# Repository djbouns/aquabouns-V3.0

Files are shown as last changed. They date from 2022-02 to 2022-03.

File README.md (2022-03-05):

# Aquabouns-V3.0

#### l'Aquabouns, le programme entièrement GRATUIT d'automatisation d'aquarium récifal.

 *-*-*-*-*
 
 *-*-*-*-* *-*-*-*-* *-*-*-*-* *-*-*-*-* *-*-*-*-* *-*-*-*-* *-*-*-*-* *-*-*-*-* *-*-*-*-* *-*-*-*-* *-*-*-*-* *-*-*-*-*
 
 *-*-*-*-*
 
###### l’Aquabouns en questions:  
> l'Aquabouns c'est quoi ? ----------------------- l'Aquabouns est un programme pour automatiser votre aquarium récifal. 
> 
> Comment ça fonctionne ?------------------------- le programme Aquabouns est prévu pour etre instalé sur une cartes arduino Mega. l'arduino communique ensuite avec différents périphériques (écran, module wifi et module GSM) et interprète l'état des différents capteurs (flotteur, sonde de température, horloge) et en fonction du paramétrage, intervient sur le matériel du bac (pompe remonté, brassage, ventilation, écumeur ...). 
> 
> Comment obtenir le programme ? à quel prix ? --- l'Aquabouns est mis a disposition GRATUITEMENT, il a été déposé sous License libre (GPL 3.0) afin que tout le monde puisse en profiter. 
> 
> Comment faire le montage ? --------------------- Tout se trouve dans les notices que vous pouvez télécharger sur www.aquabouns.fr et si le montage n'est pas à votre porté, vous pouvez vous faire aider d'un PCBouns, www.pcbouns.fr. 

 *-*-*-*-*
 
 *-*-*-*-* *-*-*-*-* *-*-*-*-* *-*-*-*-* *-*-*-*-* *-*-*-*-* *-*-*-*-* *-*-*-*-* *-*-*-*-* *-*-*-*-* *-*-*-*-* *-*-*-*-*
 
 *-*-*-*-*
 
#### Soutenez le projet pour qu'il continue d’évoluer et d’être mis à disposition gratuitement en faisant un DON

 

 *-*-*-*-*
 
 *-*-*-*-* *-*-*-*-* *-*-*-*-* *-*-*-*-* *-*-*-*-* *-*-*-*-* *-*-*-*-* *-*-*-*-* *-*-*-*-* *-*-*-*-* *-*-*-*-* *-*-*-*-*
 
 *-*-*-*-*

### Remerciements
-----------------

Cela a été possible grâce à quelques rares personnes qui m’ont aidé ou guidé quand j’en avais besoin.
Un GRAND merci à JML du forum Arduino pour son aide et tous ses conseils reçus, qui ont permis à ce projet d’être aussi abouti.
Merci à tous le forum Arduino pour son aide.
Merci à Commodore et maxime d'avoir participer a la phase de test.

Et un énorme merci a celui qui a redesigner, entre autre, toute la partie graphique de cette Aquabouns V3.0.

!!!!!!!!!! Loïc 'Solyum' D. !!!!!!!!!!

Pour voir son travail ou le contacter:
https://www.behance.net/solyum
contact: loic_dekeyser@outlook.com

 *-*-*-*-*
 
 *-*-*-*-* *-*-*-*-* *-*-*-*-* *-*-*-*-* *-*-*-*-* *-*-*-*-* *-*-*-*-* *-*-*-*-* *-*-*-*-* *-*-*-*-* *-*-*-*-* *-*-*-*-*
 
 *-*-*-*-*

### Changements apportés dans la V3.0
-------------------------------------

#### Correction de BUG
- Correction de certaines valeures qui n'etait pas mis a jour en temps reel sur l'ecran

#### Améliorations
- Re design total de la partie graphique
- Amelioration de l'utilisation de la memoire -4% soit 275 octets
- 13 ecrans Nextion compatible au lieu de 5 (serie standard, enhanced et inteligent) en resolution 800*480
- Ajout de la gestion de la temperature du bac (au lieu de juste la securiser)
- Passage de 2 (bleu, blanc) a 4 (couleur 1, couleur 2, couleur3, couleur 4) canaux independant d'éclairage
- Ajout d'un bouton "changement d'eau" qui coupe la pompe de remontée, l'osmolation, l'ecumeur et le chauffage. cela permet de vidanger sa decante et faire son changement d'eau
- Ajout d'une page dédié au parametrage de l'eclairage
- Ajout d'une page dédié au alarme
- Réglage de la luminosité de l'ecran
- Gestion de l'eclairage du refuge
- Séparation entre acalmie nocturne et acalmie nourissage pour avoir si besoin deux valeur differente
- Supression des messages d'erreur sur l'ecran principale, remplacer par un icone de notification dirigeant vers la page de visualisation des erreurs (carte SD)
- Ajout d'un bouton d'activation / desactivation du buzzer
- Choix dans la fonction du flotteur de securité, securité du niveau decante ou securité du niveau du bac (descente bouchée)
- Ajout d'un flotteur niveau haut pour la reserve d'eau
- Remplissage de la reserve d'eau osmosé avec un timer de securité (pour couper une elecrovanne)
- Choix pour l'utilisation d'une multiprise commandée (inverse le fonctionement de l'ecumeur, la pompe de remonté et le chauffage)
- Retour sur la page principale apres 1 minutes d'inactivité pour toutes les pages (sauf pour la page calibrage des sondes)
- Code pin pour deverouiller SIM
- 4 courbes graphique de mesure pour les ecrans standard (au lieu de deux precedement)
- Confirmation par pop up pour securiser certaine action sur l'ecran
- Modification des valeurs via clavier azerty ou numerique
- Possibilité de gerer un RAC via PH (en remplacement des mesure PH du bac. desactive les alarmes PH)
- Ajout d'un bouton "recovery" pour remmetre l'aquabouns au parametre d'origine
- Controlle des rampe KESSIL (A80 et A160)
- Possibiliter de configurer le nombre de clic sur le distributeur de nouriture

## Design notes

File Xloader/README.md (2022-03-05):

### Important

#### Ce logiciels as été telechargé et passé à l'antivirus, cependant, je ne pourrais être tenu responsable dans le cas où des indésirables subsisteraient.

## Pour l'instalation rapide de l'Aquabouns sur votre arduino :
* Lancer le programme Xloader 
* Utiliser le fichier .hex de votre choix disponible dans le dossier .hex

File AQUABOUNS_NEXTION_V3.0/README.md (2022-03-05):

### Vous avez la possibilité de choisir parmis plusieurs model d'ecran nextion
-----

!!! IMPORTANT !!! 

il faut imperativement utiliser un ecran nextion ORIGINAL. 

Les copies ne reconnaisent pas les fichiers 

voici quelques lien pour acheter votre écran : 
> NX8048K050
> https://amzn.to/374M18p ,
> https://amzn.to/3CfWHwh

> NX8048K070
> https://amzn.to/3hDuWED , 
> https://amzn.to/3vH1E06 , 
> https://amzn.to/3CjSxDU 

> NX8048T070 : 
> https://amzn.to/3HEMzyd

> NX8048T050 :
> https://amzn.to/3Mn7Ccn , 
> https://amzn.to/3HIcTYf

> NX8048P070 : 
> https://amzn.to/3vGS0KX ,
> https://amzn.to/3vWU0in

> NX8048P050 :
> https://amzn.to/3tzE6aL , 
> https://amzn.to/3tAiRp0 ,
> https://amzn.to/3pEDW0K ,
> https://amzn.to/3ttWgul

-----

 #### Afin de faire votre choix il faut evaluer vos besoins :
  - taille 5" ou 7"
  - version standard, enhanced ou inteligent
  - avec ou sans boitier
  - ecran resistif ou capacitif

  ##### Le principe de l'écran tactile résistif : 
  
  - Un écran résistif est constitué de deux surfaces séparées par de minuscules entretoises et parcourues de connecteurs.
  Le touché du doigt ou d'une pointe quelconque déforme la surface supérieure et met en contact ses connecteurs avec ceux de la surface intérieure. L'utilisation d'un stylet est souvent necessaire.
  - Un écran tactile capacitif : Quand le doigt, conducteur d'électricité, touche l'écran, des charges électriques lui sont transférées.
-----
  ### voici les models compatibles avec l'Aquabouns V3 :
-  ecran 5" NX8048P050-011R <<< version inteligent resistif
-  ecran 5" NX8048P050-011C <<< version inteligent capacitif
-  ecran 5" NX8048P050-011R <<< version inteligent resistif
-  ecran 5" NX8048P050-011C <<< version inteligent capacitif
- ecran 7" NX8048P070-011R <<< version inteligent resistif
-  ecran 7" NX8048P070-011C <<< version inteligent capacitif
-  ecran 7" NX8048P070-011R <<< version inteligent resistif
-  ecran 7" NX8048P070-011C <<< version inteligent capacitif
-  ecran 5" NX8048T050_011R <<< version standard resistif
 - ecran 7" NX8048T070_011R <<< version standard resistif
- ecran 5" NX8048K050_011R <<< version enhanced resistif
- ecran 7" NX8048K070_011R <<< version enhanced resistif
-  ecran 7" NX8048K070_011C <<< version enhanced capacitif

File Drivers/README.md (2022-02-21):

#### Si votre matériel n'est pas reconnu par votre système d'exploitation, installer le driver correspondant (voir sur votre carte)
-----
### Important

#### Ces logiciels ont été telechargés et passés à l'antivirus, cependant, je ne pourrais être tenu responsable dans le cas où des indésirables subsisteraient.

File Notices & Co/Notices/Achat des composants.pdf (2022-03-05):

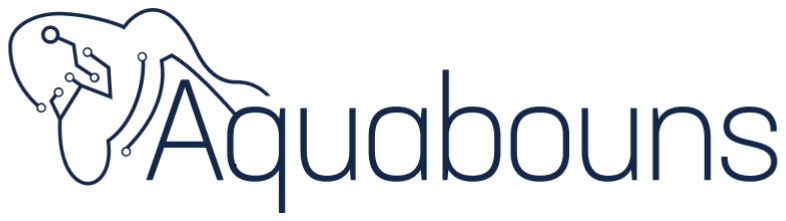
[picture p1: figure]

Page 1 sur 7

## Liste des composants nécessaires à la fabrication d’un

Maj 05/03/22

Bonjour,

Je vous ai fait une liste de tous les composants nécessaires pour la fabrication d’un Aquabouns a partir du site Amazon.

Si le montage d’un Aquabouns n’est pas à votre porté, vous pouvez vous faire aider d’un PCBouns, Plus d’infos sur www.pcbouns.fr

## Périphériques nécessaires :

Arduino Méga ORIGINAL :
https://amzn.to/3veW5me

Arduino Méga copie :
https://amzn.to/3mWXMCV *
https://amzn.to/3eTTCXS *

Module GSM SIM800L V2.0 :
https://amzn.to/3BBnBxJ
https://amzn.to/3F8JRjz
https://amzn.to/31stdxt
https://amzn.to/2TdiItm

Module Wifi Wemos d1 mini : https://amzn.to/3fcP53Q *
https://amzn.to/2WLyHk3
https://amzn.to/3taT0DH

Lecteur de Carte SD :
https://amzn.to/3tx2g5D *

Page 2 sur 7

https://amzn.to/3yuAVmd

Horloge DS3231 :
https://amzn.to/3vbAD1y
https://amzn.to/3yEDXDd

Sonde de température DS18B20 : https://amzn.to/3fHNzG3
https://amzn.to/345TsHJ *
https://amzn.to/348vw6E

Relais ( 4 ) :
https://amzn.to/3EVuNpc
https://amzn.to/3eTVNuw *

Relais ( 8 ) :
https://amzn.to/3yGkDWu *
https://amzn.to/3mWv1XF
https://amzn.to/3BIoDrn

Buzzer 5V Passif :
https://amzn.to/3fcVJaw

Flotteurs :
https://amzn.to/3gZ8GVT
https://amzn.to/3hMzYzK *

Alimentation 5V, 4A, 8A et 10A : https://amzn.to/3wmbCAQ
https://amzn.to/3v7bntn
https://amzn.to/3yuUpav *

Alimentation 12V 5A ou 10A (Pour alimenter pompe d'osmolation, ventilateur, ect...) : https://amzn.to/3v8sYB8 *
https://amzn.to/2ScIa1z

## Ecran Nextion :

NX8048K050 :
https://amzn.to/374M18p
https://amzn.to/3CfWHwh

NX8048K070 :
https://amzn.to/3hDuWED
https://amzn.to/3vH1E06
https://amzn.to/3CjSxDU

NX8048T070 :
https://amzn.to/3HEMzyd
NX8048T050 :
https://amzn.to/3Mn7Ccn

Page 3 sur 7

https://amzn.to/3HIcTYf

NX8048P070 :
https://amzn.to/3vGS0KX
https://amzn.to/3vWU0in

NX8048P050 :
https://amzn.to/3tzE6aL
https://amzn.to/3tAiRp0
https://amzn.to/3pEDW0K
https://amzn.to/3ttWgul

## Composants nécessaires dans le tuto montage sur shield a borniers ou sur la notice de montage :

Shield Arduino méga avec bornier à vis :
https://amzn.to/3vcR1yY *
https://amzn.to/38DICuM

Des pins mâle et femelle :
https://amzn.to/3oEsJeJ
https://amzn.to/3vdSKUL

Des connecteurs male femelle pour relais ou module Atlas : https://amzn.to/3uaj0xX *
https://amzn.to/2T73UMJ

Condensateurs :
https://amzn.to/3HCOML3
https://amzn.to/3jEFc12
https://amzn.to/3vdLJTJ
https://amzn.to/2WV8fVs
https://amzn.to/3vijiUY
https://amzn.to/34oON76
https://amzn.to/3JKDsyg
https://amzn.to/3udMaMB
https://amzn.to/3n3kyd5

Circuit imprimé de prototypage : https://amzn.to/3oFyVTD
https://amzn.to/2Sf2CPm

Résistances 4.7k Ohms 1/4w : https://amzn.to/2QF2yIc
https://amzn.to/3wqTYMC

Résistances 3.3k Ohms 1/4w : https://amzn.to/3hI1iPL
https://amzn.to/2SlI87q
Lot de résistances :
https://amzn.to/3mK7esf

Page 4 sur 7

https://amzn.to/3faOCPL
https://amzn.to/3DNq7Sj

Du fil ou des jumper :
https://amzn.to/3f8Gq2f *
https://amzn.to/3asSsjZ
https://amzn.to/3oDUZhD
https://amzn.to/3v7Tafc
https://amzn.to/2Siy4vY

## Outillages :

Un fer ou une station à souder : https://amzn.to/3eTJvCE
https://amzn.to/3pT7yIa
https://amzn.to/3BFjHDo *
https://amzn.to/3yFiknR *

Un ventilateur (pour éviter de respirer les vapeurs de soudure très nocive) : https://amzn.to/3pXkxIWhttps://amzn.to/343QZgW
https://amzn.to/3wHJ4CN *

De l’étain :
https://amzn.to/38DlRHk
https://amzn.to/3ucgmYg *

Une 3e main :
https://amzn.to/345hx1l *
https://amzn.to/3qIVh88 *
https://amzn.to/2QF7nRM *
https://amzn.to/3HFiDCO

Tapis de protection :
https://amzn.to/32QO663 *
https://amzn.to/345SMlo
https://amzn.to/3mTRTX2

Un multimètre :
https://amzn.to/34d3n1g *
https://amzn.to/3wqqTAL *
https://amzn.to/3u9Vi4P

Pince à dénuder :
https://amzn.to/3wslp8y
https://amzn.to/3yIxck3 *
https://amzn.to/3oHEGR2
https://amzn.to/3cG0qb5 *

## Autres Périphériques :

Page 5 sur 7

Chargeur de batterie NiMh : https://amzn.to/34lM6QB
https://amzn.to/2QGrJtY

Batterie NiMh 7.2V de 2000mAh a 4500mAh : https://amzn.to/3wppomR *
https://amzn.to/347gwFR

Chargeur de batterie lithium : https://amzn.to/2SBh6JA (https://l.facebook.com/l.php?__tn__=-UK-R)
https://amzn.to/3fA2qna

Batterie lithium:
https://amzn.to/3i9KyRP (https://l.facebook.com/l.php?__tn__=R%5d-R)
https://amzn.to/3fUeDC6 (https://amzn.to/3fUeDC6?fbclid=IwAR3H6U5Kd28EvL8qs_eYgOksjzHbHOwAQY4HB5FtiXMJWDR3tEAGBMP98k8)

Circuit imprimé d’alimentation à partir d’une alimentation de PC : https://amzn.to/3fZQnyg
https://amzn.to/3qNS8Ec

Convertisseur DC-DC 4A (Pour convertir le 12V ou la batterie en 5V par exemple) : https://amzn.to/3sXQL8E
https://amzn.to/3DK1ypV

Convertisseur PWM 5V/10V
https://amzn.to/2Sk3baM *
https://amzn.to/2QLDQ9g *
https://amzn.to/3oV6MKK

Pompe d'osmolation 12v :
https://amzn.to/3bMSrsf
https://amzn.to/3vgshpm | *
https://amzn.to/348ysjG | *

Ventilateur d'aquarium ventilateur 12V : https://amzn.to/2SgpU7E
https://amzn.to/3pyhCEx *
https://amzn.to/3fCgY4h
https://amzn.to/3zrAHNC

Sonde PH :
https://amzn.to/3fFML4m *
https://amzn.to/3uczDJo
https://amzn.to/3fdR8Vw *
https://amzn.to/3fb2cmj

Solution étalon PH :
https://amzn.to/3f9OHTz
https://amzn.to/3494tYE

Sonde ORP :

Page 6 sur 7

https://amzn.to/3oJtp2C *
https://amzn.to/3u7dRGJ

Solution étalon ORP :
https://amzn.to/3484qfH
https://amzn.to/3fzf0lg

Rallonge BNC :
https://amzn.to/2WUTr9n
https://amzn.to/3vdiosJ *

## Eclairage :

Driver LED Meanwell Dimmable: https://amzn.to/3f9BLgI
https://amzn.to/3wwyP3D *

## Brassage :

Pompe TUNZE Turbelle nanostream : https://amzn.to/3oEm1pb
https://amzn.to/3yqMBGN *
https://amzn.to/3u6Rb9P *
https://amzn.to/3pVWSZp

Cable DIN 5 (Pour se brancher sur le boitier de contrôle TUNZE) : https://amzn.to/3vhYc92 *

Pompe de brassage JEBAO :
https://amzn.to/3HApInP
https://amzn.to/3qMJq9q
https://amzn.to/2QLCyLs *

Contrôleur brushless (Pour contrôler toutes pompes à moteur brushless) : https://amzn.to/345EVf2
https://amzn.to/3n0vCI6

Oscillateur :
https://neo3plus.com/fr/accessoires/203-oscillateurs-de-pompes-osci.html *

## MESURES :

Module Atlas Scientific :
https://www.whiteboxes.ch/cart/ >>> Avec le code AQUABOUNS-2021 vous avez -10% sur votre commande

Les Liens suivis de * Correspondent à du matériel que j’utilise ou ai utilisés

Page 7 sur 7

### Si le montage d’un Aquabouns n’est pas à votre porté, vous pouvez vous faire aider

d’un PCBouns, Plus d’infos sur www.pcbouns.fr

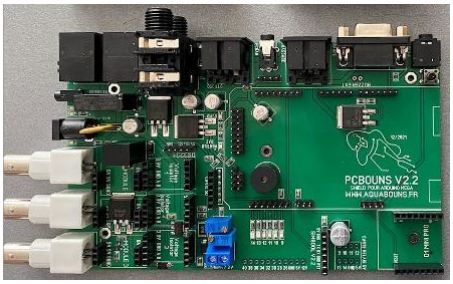
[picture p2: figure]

Soutenez le projet pour qu'il continue d’évoluer et d’être mis à disposition gratuitement en faisant un DON

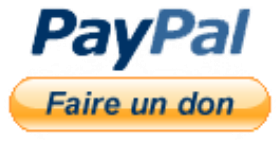
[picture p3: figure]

N’hésitez pas à me contacter :

www.facebook.com/aquabouns ou contact@aquabouns.fr

Profiter bien de cet automate et venez partager vos impressions, vos expériences, vos remarques, vos idées sur le groupe FACEBOOK

https://www.facebook.com/groups/aquabouns/

## DJBOUNS 2022

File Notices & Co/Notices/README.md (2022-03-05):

## Dans l'attente de finalisation de la notice V3,je vous propose :
* Pour la partie instalation du programmed'utiliser la notice V2 .
* Pour la partie instalation rapide, suivez les instructions de l'imprime ecran de Xloader
* Pour la partie utilisation de la V3, vous pouvez regarder la video de presentation : https://www.youtube.com/watch?v=JMc6JZke7Aw

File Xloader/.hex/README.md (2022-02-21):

# Affectation des pins pour les fichiers d'instalation simplifiées

Les fichiers d'installations simplifiées ont été configurées en affectant les pins en fonction de votre montage :

#### > Affectation version PCBouns 1.5, 1.6 et 2.0 faite conformement au PCBouns utilisé.
-----
#### > Affectation version utilisateur : 

// entrées/sorties analogique
* hardResetWIFI = A5
* hardResetGSM = A6
* pinInCoupureCourant = A7
* pinInBatterie = A8
* pinOutRelaisChauffage = A10
* pinOutRelaisEcumeur = A11
* pinOutRelaisRemontee = A13

// entrées/sorties digital
* pinOutBrassage = 2, 3, 4
* pinOUTOscillo1 = 5
* pinOUTOscillo2 = 6
* pinOUTOscillo3 = 7
* pinOutRelaisVentilateurRampe = 8
* pinOutEclairage = 11, 12, 9, 10
* pinInSondeDs18b20 = 13
* nextion = Serial1
* gsm = Serial2
* d1mini = Serial3
* sda > ds3231 + 3x MODUL ATLAS = 20
* scl > ds3231 + 3x MODUL ATLAS = 21
* pinInFlotteurGodetEcumeur = 27
* pinOutRelaisRefuge = 28
* pinInFlotteurReserveBas = 29
* pinOutRelaisRemplissageReserve = 30
* pinInFlotteurReserveHaut = 31
* pinOutRAC = 32
* pinInFlotteurOsmolation = 33
* pinInFlotteurNiveauEcumeur = 35
* pinOutRelaisDistributeurNouriture = 37
* pinInFlotteurSecurite = 39
* pinOutBatterie = 41
* pinOutRelaisVentilateurBac = 47
* pinOutbuzzer = 48
* pinOutRelaisOsmolation = 49;
* miso > carte sd = 50
* mosi > carte sd = 51
* sck > carte sd = 52
* cs > carte sd = 53
-------
#### > Affectation version PCBouns MINI 1.0 : 

// entrées/sorties analogique
* hardResetWIFI = A0
* hardResetGSM = A1
* pinOutRelaisChauffage = A2
* pinOutRelaisEcumeur = A3
* pinOutRelaisRemontee = A4
* pinOutRelaisVentilateurRampe = A5
* pinOutRelaisDistributeurNouriture = A6
* pinOutRelaisVentilateurBac = A7
* pinOutRelaisOsmolation = A8
* pinOutBatterie = A9
* pinInBatterie = A10
* pinOutRelaisRefuge = A11
* pinOutRelaisRemplissageReserve = A12
* pinOutRAC = A13

// entrées/sorties digital
* pinOutBrassage = 2, 3, 4
* pinOUTOscillo1 = 5
* pinOUTOscillo2 = 6
* pinOUTOscillo3 = 7
* pinOutEclairage = 8, 9, 10 , 11
* pinInSondeDs18b20 13
* nextion Serial1
* d1mini Serial2
* gsm Serial3
* sda > ds3231 + 3x MODUL ATLAS = 20
* scl > ds3231 + 3x MODUL ATLAS = 21
* pinInCoupureCourant = 22
* pinInFlotteurGodetEcumeur = 24
* pinInFlotteurReserveBas = 25
* pinInFlotteurOsmolation = 26
* pinInFlotteurNiveauEcumeur = 27
* pinInFlotteurSecurite = 28
* pinInFlotteurReserveHaut = 29
* pinOutbuzzer = 49
* miso > carte sd = 50
* mosi > carte sd = 51
* sck > carte sd = 52
* sc > carte sd = 53
-------
## Le reste de la configuration a été faite tel que :

// Choix du mode inversé pour l'eclairage
* PWMinverse = OFF

// Utilisation d'une rampe Kessil
* kessil = OFF

// nombre de clic manuel sur le distributeur de nouriture
* nombre2ClicDistributeur = 1

// Utilisation d'une multiprise commandée
* multiPrise = OFF

// Choix du mode du flotteur securité
* secuDec = ON
* secuBac = OFF
-------
## Pour toute autre configuration :

Vous devrez configurer le fichier "AQUABOUNS_MEGA_V3.0.ino" selon vos besoins puis utiliser la methode classique pour instaler le programme dans l'arduino.
En cas de grosse difficulté, contacter moi.

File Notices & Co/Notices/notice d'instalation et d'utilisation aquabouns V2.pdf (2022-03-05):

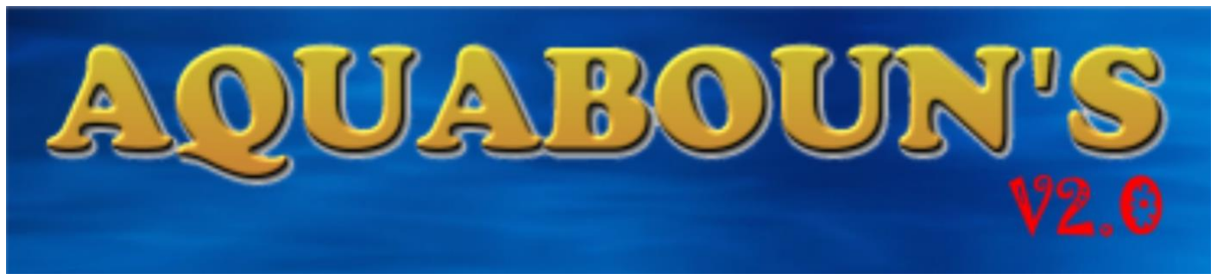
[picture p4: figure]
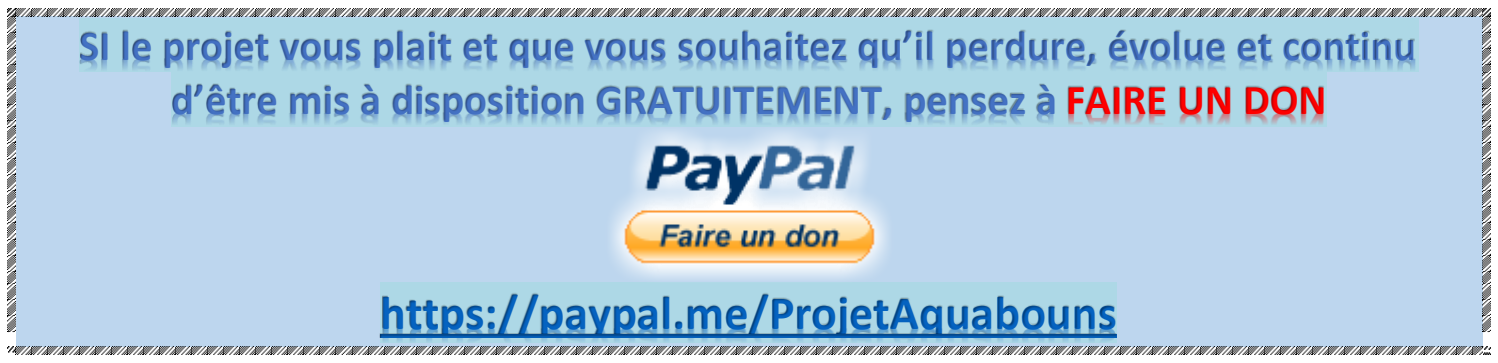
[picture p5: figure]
https://paypal.me/ProjetAquabouns

Page 1 sur 39

# Automate de gestion d’aquarium récifal

## Par DJBOUNS

MAJ 15/10/21

Bonjour,

Ce projet a débuté en Mai 2017 dans l’intention de réaliser un automate pour aquarium récifal complet, fiable et à faible coût pour qu’un maximum de récifalistes puissent en profiter.

Il verra le jour grâce à quelques rares personnes qui m’ont aidé ou guidé quand j’en avais besoin.
Un GRAND merci à JML du forum Arduino pour son aide et tous ses conseils reçus, qui ont permis à ce projet d’être aussi abouti.
Merci à tous le forum Arduino pour son aide.
Merci à Commodore pour sa participation dans le développement de cette V2.0

AQUABOUN’S représente des milliers d'heures de travail pour ~6000 lignes de code, 1000 lignes de plus que la V1.0.
Cela représente également des dépenses importantes pour tester et trouver le matériel le plus adapté. Il est mis à disposition entièrement gratuitement afin que tout le monde puisse profiter d’un automate à faible coût.
Vous pouvez le télécharger à partir du site : WWW.AQUABOUNS.FR

N’hésitez pas à me faire part de toute amélioration ou évolution souhaitées : www.facebook.com/aquabouns ou contact@aquabouns.fr

## SI le projet vous plait et que vous souhaitez qu’il perdure, évolue et continu d’être mis à disposition GRATUITEMENT, pensez à FAIRE UN DON

### Merci et bon montage à tous

Page 2 sur 39

# SOMMAIRE

I. Installation du programme | Page 3
1. Installation de l’IDE Arduino et ses librairies | Page 3
2. Installation de l’AQUABOUNS sur l’Arduino Méga | Page 4
3. Installation de l’AQUABOUNS sur l’ESP | Page 7
4. Installation de l’AQUABOUNS sur l’écran Nextion | Page 8
II. Notice d’utilisation | Page 9
1. Page de démarrage | Page 9
2. Page d’accueil | Page 12
3. Page calibration | Page 15
4. Page brassage | Page 16
5. Page choix du graphique | Page 18
6. Page graphique 24h ou 7 jours | Page 19
7. Page paramétrage | Page 20
8. Page GSM | Page 25
9. Page WIFI | Page 26
10.Page Horloge | Page 27
11. Page SD | Page 28
12.Page info | Page 29
13.Page fonctions en arrière-plan | Page 30
14.Page Web | Page 32
Exemple pour Box Bouygues | Page 33
Exemple pour Freebox Crystal | Page 35
IV. A bientôt | Page 39

Page 3 sur 39

# I. Installation du programme :

## !!! ATTENTION !!!

Je ne suis pas informaticien ni programmateur. Ce programme a été réalisé avec le plus de soins possibles, cependant, il n’est pas exclu que des bugs subsistent.
Ne pas laisser sans surveillance. Djbouns décline toute responsabilité quant aux dommages directs ou indirects qui pourraient être causés.

### 1. Installation de l’IDE Arduino et de ses librairies

a) Installez l’IDE Arduino : https://www.arduino.cc/en/Main/Software
b) Lancez l’IDE Arduino
c) Téléchargez la pack AQUABOUNS : https://github.com/djbouns/aquaboun-s
d) Le pack contient un dossier « libraries » regroupant toutes les bibliothèques nécessaires, copier son contenu dans le dossier « libraries » de l’installation Arduino, normalement :
C:\Users\VOTRE NOM D’UTILISATEUR\Documents\Arduino\libraries
!!! ATTENTION !!!
Vous devez utiliser ces versions de librairies. Refuser toute mise à jour proposée par l’IDE Arduino, au risque de ne plus pouvoir installer le programme.
e) Copiez les dossiers AQUABOUNS_MEGA_V*.* et AQUABOUNS_WIFI_V*.* dans : C:\Users#UserName#\Documents\Arduino\
f) Copiez le dossier « tools » dans :
C:\Users#UserName#\Documents\Arduino\
g) Dans l’IDE Arduino, allez dans fichier/préférences et dans le champ « URL de gestion de carte supplémentaires » ajouter : http://arduino.esp8266.com/stable/package_esp8266com_index.json
h) Aller dans outils, type de carte, gestionnaire de carte. Dans recherche taper « ESP ». Vous allez avoir ESP8266 choisissez la version 2.5.0 et installer (les versions suivantes ne fonctionnent pas (Vous aurez des erreurs de compilation))

### 2. Installation du programme sur l’Arduino méga :

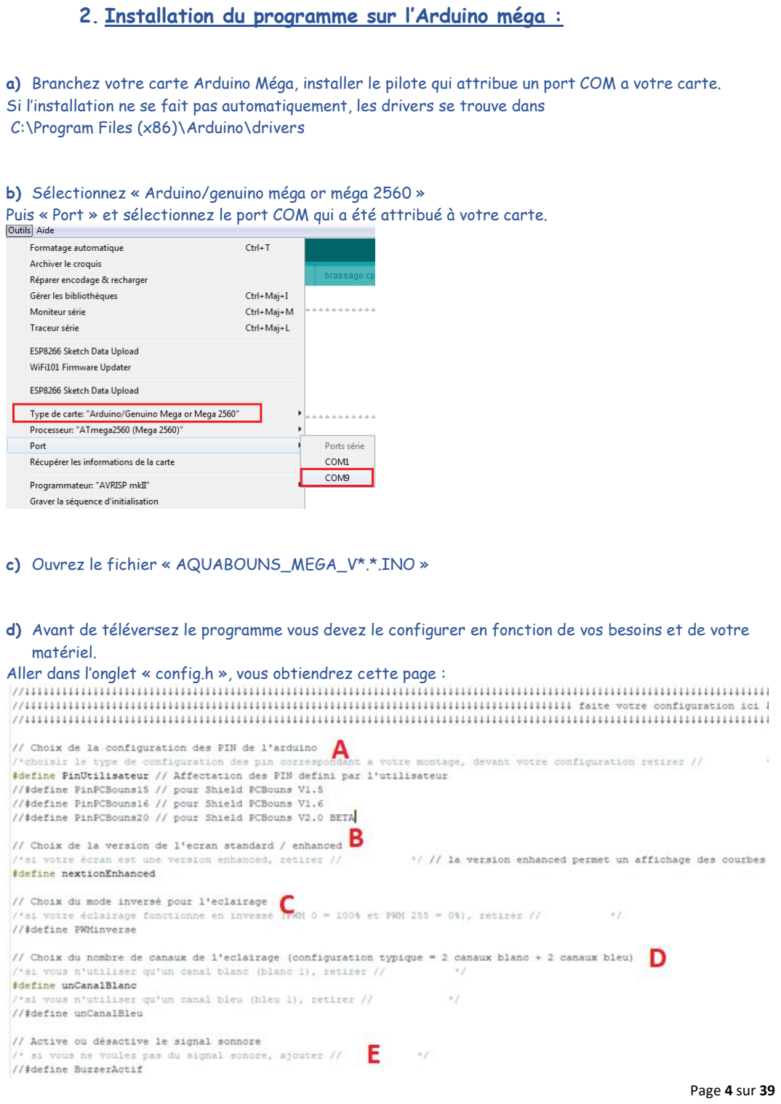
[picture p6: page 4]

Page 4 sur 39

a) Branchez votre carte Arduino Méga, installer le pilote qui attribue un port COM a votre carte. Si l’installation ne se fait pas automatiquement, les drivers se trouve dans
C:\Program Files (x86)\Arduino\drivers
b) Sélectionnez « Arduino/genuino méga or méga 2560 »
Puis « Port » et sélectionnez le port COM qui a été attribué à votre carte.
c) Ouvrez le fichier « AQUABOUNS_MEGA_V*.*.INO »
d) Avant de téléversez le programme vous devez le configurer en fonction de vos besoins et de votre matériel.
Aller dans l’onglet « config.h », vous obtiendrez cette page :

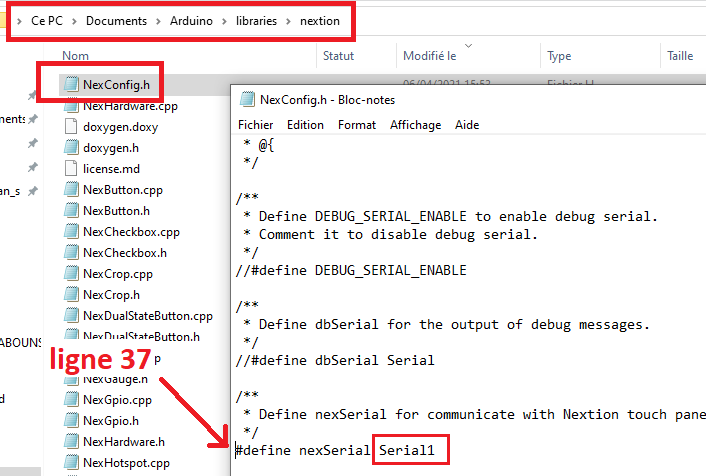
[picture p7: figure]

Page 5 sur 39

A. Choix de la configuration des Pins de l'Arduino
Vous devez choisir la configuration des Pins que vous utilisez sur 4 choix :
- #define PinUtilisateur // Affectation des PIN défini par l'utilisateur
- #define PinPCBouns15 // pour Shield PCBouns V1.5
- #define PinPCBouns16 // pour Shield PCBouns V1.6
- #define PinPCBouns20 // pour Shield PCBouns V2.0 BETA
Mettre // devant les configurations non utilisées.
Il ne doit y avoir qu’une des quatre lignes ne commençant pas par // Exemple pour utiliser les pins définis par l’utilisateur :

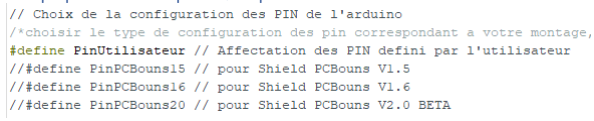
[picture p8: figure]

Important,
Si vous utilisez #define PinUtilisateur, vous devez modifier l’affectation des Pins dans l’onglet PinUtilisateur.h pour les faire correspondre à votre montage (plus d’infos sur la notice de montage)

!!! TRES IMPORTANT !!!

L’AQUABOUNS et l’écran communique via un port série de votre choix que vous devez déclarer dans le logiciel, MAIS AUSSI dans la bibliothèque Nextion, ligne 37 du fichier NexConfig.h, sans quoi la communication ne se feras pas.

Exemple ci-dessous, Nextion déclaré en Serial1 : (choix possible Serial1, Serial2 ou Serial3) :

Page 6 sur 39

B. Choix de la version de l'écran standard / enhanced
Si vous utilisez un écran en version Standard vous devez ajouter // devant #define nextionEnhanced

Important,
Une version standard permet un affichage des courbes de température et Ph Une version enhanced permet un affichage des courbes de température, Ph, redox et salinité
C. Choix du mode inversé pour l'éclairage
Si vos drivers LED fonctionnes à l’inverse (PWM 0% = LED a 100% et PWM 100% = LED a 0) vous devez retirer // devant #define PWMinverse
D. Choix du nombre de canaux de l'éclairage
Si vous voulez utilisez qu’un seul canal blanc ou bleu, retirer // devant #define unCanalBlanc et/ou devant #define unCanalBleu
E. Active ou désactive le signal sonore
Si vous ne souhaitez pas activer le signal sonore des alertes ajouter // devant #define BuzzerActif
e) Cliquez sur téléverser :

Le logiciel compile le programme puis le téléverse.
Cela prend ~1 minutes
Si tout s’est bien passé, débranchez le câble USB, votre Arduino est programmé. Dans le cas contraire, vérifiez toutes les étapes à partir de 2.

Page 7 sur 39

### 3. Installation du programme sur l’ESP :

a) Branchez votre carte Wifi, l’installation du pilote se fait automatiquement et attribut un port COM a votre carte.
(Lors des étapes suivantes, la carte Wifi ne doit pas être reliée à l’Arduino)
b) Sélectionnez la carte Wifi « D1 mini Lite »

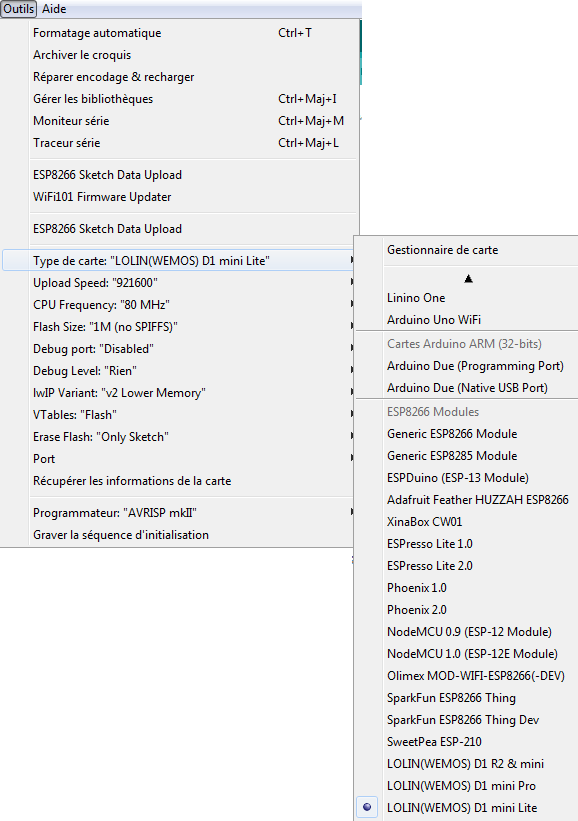
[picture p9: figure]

Dans « Port » et sélectionnez le port COM qui a été attribué à votre carte.

c) Ouvrez le fichier « AQUABOUNS_WIFI_V*.*.INO »
d) Cliquez sur téléverser :

Le logiciel compile le programme puis le téléverse. Cela prend ~1 minutes
Si tout s’est bien passé, passez à l’étape suivante. Dans le cas contraire, vérifiez les étapes à partir de 1>

Page 8 sur 39

e) Vérifiez que la mémoire flash attribuée est égale ou supérieure à 256K

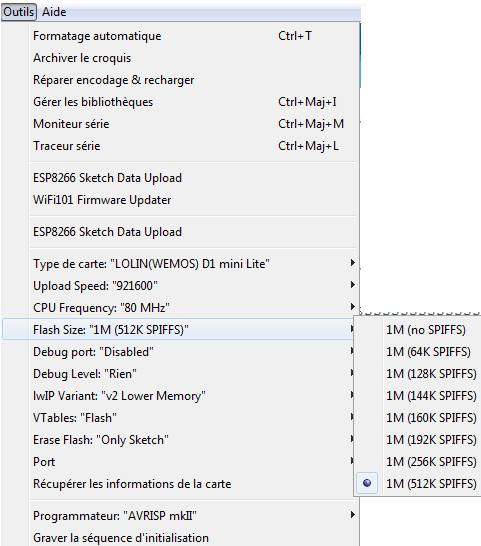
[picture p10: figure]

f) Cliquez sur « ESP8266 Sketch Data Upload » pour téléverser tous les fichiers (page web) dans la mémoire flash
Le temps de téléversement dépend de la taille de mémoire attribuée.
Si tout s’est bien passé, débranchez le câble USB, votre carte Wifi est programmée.
Dans le cas contraire, vérifiez les étapes à partir de 2.

### 4. Installation du code sur l’écran Nextion

a) Dans le dossier AQUABOUNS_NEXTION_V*.* copiez le fichier correspondant à votre écran (taille et version) « nextion Aquabouns *’’ *****.tft » sur une carte Micro SD formater en Fat 32.
b) Insérez la carte Micro SD dans l’écran Nextion puis allumez-le.
c) Le chargement du fichier prend un peu de temps …
d) Une fois le chargement réussi, éteignez l’écran et retirez la carte Micro SD
e) L’écran est opérationnel.

### Si toutes ces étapes se sont correctement passées, vous pouvez assembler les cartes et lancer l’AQUABOUN’S 😊

# II. Notice d’utilisation :

## !!! ATTENTION !!!

Page 9 sur 39

Je ne suis pas informaticien ni programmateur. Ce programme a été réalisé avec le plus de soins possibles, cependant, il n’est pas exclu que des bugs subsistent.
Ne pas laisser sans surveillance. Djbouns décline toute responsabilité quant aux dommages directs ou indirects qui pourraient être causés.

### 1.Page de démarrage :

Ci-dessus, l’écran indiquant une initialisation réussie de tous les modules

A. Importe les paramètres sauvegardés dans l’eeprom :

Si aucun paramètre n’est importé :

Si les paramètres sont correctement importés :

Page 10 sur 39

B. Initialise l’horloge :

Si l’horloge n’est pas détectée :

Si l’horloge est détecté mais n’a jamais été initialisé ou plus de batterie :

Si l’horloge est détectée :

C. Initialise les sondes de température :

Si aucune sonde n’est détectée :

Si une seule sonde est détectée, le message suivant apparaitra :

Si les deux sondes sont détectées :

D. Initialise le lecteur de carte SD :

Si le lecteur n’est pas détecté, le message suivant apparaitra :

Si le lecteur est bien détecté :

Puis on lance l’importation du SSID WIFI, MDP WIFI et Numéro de téléphone : Si les fichiers sont trouvés, les messages suivants apparaitront successivement :

Si un fichier n’est pas trouvé :

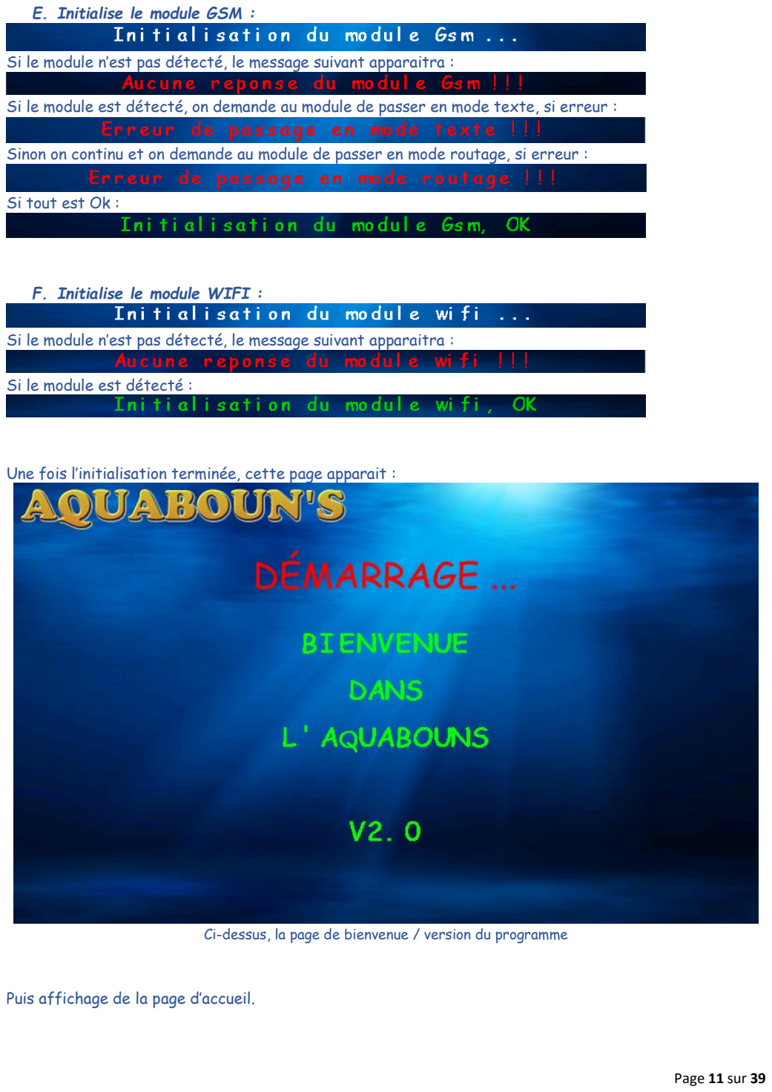
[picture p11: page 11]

Page 11 sur 39

E. Initialise le module GSM :

Si le module n’est pas détecté, le message suivant apparaitra :

Si le module est détecté, on demande au module de passer en mode texte, si erreur :

Sinon on continu et on demande au module de passer en mode routage, si erreur :

Si tout est Ok :

F. Initialise le module WIFI :

Si le module n’est pas détecté, le message suivant apparaitra :

Si le module est détecté :

Une fois l’initialisation terminée, cette page apparait :

Ci-dessus, la page de bienvenue / version du programme

Puis affichage de la page d’accueil.

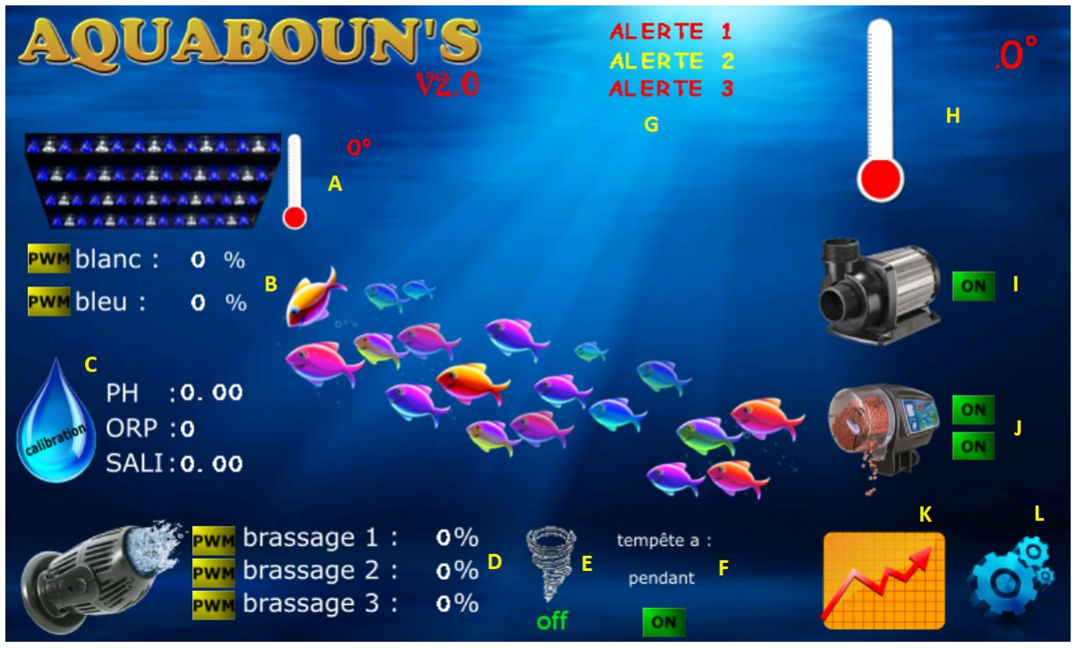
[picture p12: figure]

Page 12 sur 39

### 2.Page d’accueil :

Ci-dessus, l’écran d’accueil

A. Température de la rampe :
Indique la température de la rampe et fait varier le thermomètre proportionnellement.
>Si la température dépasse la température de ventilation paramétrée, la ventilation sera activée et l’icône suivant apparaitra :
B. Eclairage :
3 possibilités de réglage, en cliquant sur l’icône devant le canal concerné :

= puissance paramétrée

= éteint

= puissance en fonction du lever/coucher paramétré. Zénith = puissance paramétrée En bout de chaque ligne, la puissance actuelle du canal

C. Ph / Redox / Salinité :
- Affiche le Ph du bac
>Si le Ph du bac est en dessous du Ph bas paramétré ou au-dessus du Ph haut paramétré, une alarme sonore retentira, un message d’alerte s’affichera à l’écran et vous recevrez un SMS indiquant l’anomalie et le Ph actuel du bac.
- Affiche le potentiel Redox
- Affiche la salinité
En cliquant sur la goute « calibration » vous arrivez sur la page d’étalonnage des sondes

Page 13 sur 39

D. Brassage :
3 possibilités de réglage, en cliquant sur l’icône devant le canal concerné :

= puissance paramétrée

= éteint

= si la puissance d’accalmie nocturne / alimentation est paramétré, le brassage sera progressif avec le lever / coucher, au max durant le zénith et au « max – accalmie » durant la phase nocturne
En bout de chaque ligne, la puissance actuelle du canal.
En cliquant sur la pompe vous arrivez sur la page de paramétrage du brassage
E. Tempête manuelle :
Un clic sur l’icône tempête déclenche une tempête manuelle et l’icône change pour celui-ci :

La durée et puissance de la tempête son paramétrable. Un autre clic sur l’icône arrête la tempête.

F. Tempête quotidienne aléatoire :
En cliquant sur , vous activez la tempête aléatoire quotidienne. La tempête aura lieu de manière aléatoire forcement durant le zénith. La durée sera entre 10% et 100% la durée paramétrée
La puissance de la tempête sera la puissance paramétrée.
La tempête aléatoire n’aura lieu qu’une fois par jour.
L’heure et la durée de la tempête du lendemain seront générées automatiquement et affichées après la tempête du jour.
Quand la tempête est en cours, l’icône suivant apparait :
G. Message
3 lignes affichants les messages d’anomalies éventuelles.

Page 14 sur 39

H. Température du bac :
Indique la température du bac et fait varié le thermomètre proportionnellement.
>Si la température dépasse la température de ventilation paramétrée, la ventilation sera activée et l’icône suivant apparaitra :

>Si la température mesurée est sous la température basse paramétrée ou au-dessus de la température haute paramétré l’icône suivant apparaitra :

Une alarme sonore retentira, un message d’alerte s’affichera à l’écran et vous recevrez un SMS indiquant l’anomalie et la température actuelle du bac.
I. Pompe de remontée :
3 possibilités de réglage, en cliquant sur l’icône devant le canal concerné :

= marche

= éteint
= La pompe de remonté sera éteinte pendant toute la durée d’alimentation
J. Alimentation :
2 modes d’alimentation :
- Automatique :
Possibilité de 2 distributions automatiques quotidiennes si en « ON » Les heures de distribution sont paramétrables.
- Manuelle :
Un clic sur l’icône déclenche l’alimentation manuelle.
Un second clic arrête le mode alimentation.
Quel que soit le mode d’alimentation, si la puissance d’accalmie nocturne/alimentation est paramétrée, le brassage sera réduit durant la durée d’alimentation paramétrée.
Si la pompe de remontée est en mode Delay, elle sera éteinte pendant toute la durée d’alimentation.
K. Pour aller vers la page de choix des graphiques.
L. Pour aller vers la page paramétrage.

Sauvegarde des modes :
L’état des modes ON/OFF/PWM/RELAY des fonctions éclairage, brassage, tempête aléatoire, nourrissage automatique et remontée sont sauvegardés en même temps que les paramètres de la page paramétrage. En cas de redémarrage, l’AQUABOUNS réutilisera les modes sauvegardés pour chacune des fonctions.

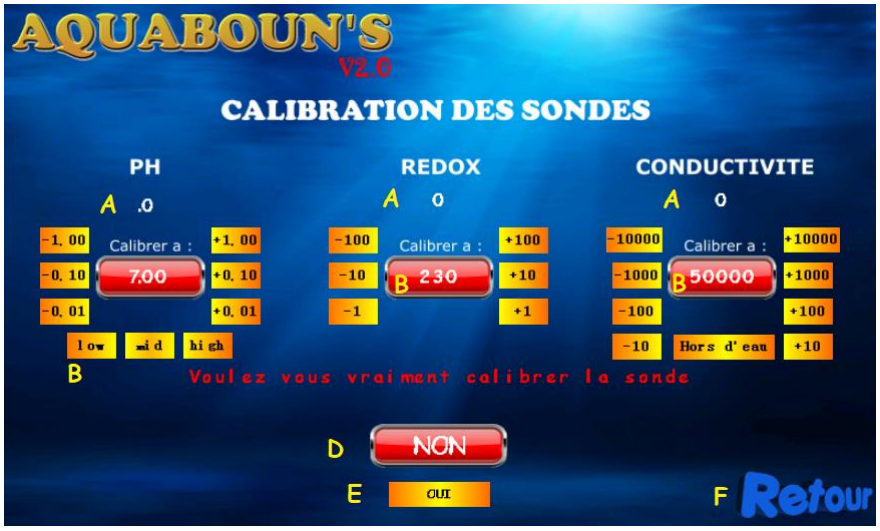
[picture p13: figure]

Page 15 sur 39

### 3.Page Calibration

A. Mesures faite pas les sondes
B. Valeur a calibré :
Ajuster la valeur à calibrer à l’aide des boutons + ou – jusqu’à obtenir la valeur correspondante à votre solution étalon.
Lorsque les 3 valeurs sont identiques (Valeur mesurée, la valeur à calibrer et valeur de la solution étalon) cliquez sur le bouton rouge indiquant la valeur à calibrer ou pour le PH sur le bouton low, mid ou high.
Un message vous indique que vous allez calibrer la sonde
Choisissez OUI ou NON
C. Calibration hors d’eau
La sonde de conductivité a besoin d’un étalonnage hors d’eau (à sec) En cliquant sur « Hors d’eau » cela lanceras cette calibration
D. Bouton NON
Annule la demande de calibration
E. Bouton OUI
Calibre la sonde à la valeur demandée
F. Retour vers la page MENU

Page 16 sur 39

### 4.Page Brassage

A. Puissance de démarrage :
Puissance à laquelle la pompe de brassage démarre
Réglable de 0 à 254
Les pompes ne démarrent pas à 1%. Il est donc nécessaire de renseigner la puissance à laquelle elles démarrent pour que le 0% = arrêt et 1% = démarrage (exemple JEBAO démarrage vers 60 sur 254, TUNZE démarrage vers 120 sur 254)
Vous devez donc régler ce paramètre = démarrage de la pompe -1
(Votre pompe démarre a 79, vous devez régler a 78)
B. Puissance :
Puissance maximum du brassage par canal
Paramétrable par canal de 0% à 100% par tranche de 5%.
C. Angle Mini :
Paramétrable par canal de 0° a (angle maxi-1°)
D. Angle Maxi :
Paramétrable par canal de (angle mini+1°) à 179°

Page 17 sur 39

E. Angle actuel :
Indique l’angle actuel de l’oscillateur.
Lorsque le paramétrage d’un angle est modifié, l’oscillateur va à cette position pour permettre de visualiser le nouveau paramétrage.
F. Vitesse de déplacement : Paramétrable de 0 seconde à 60 secondes Si paramétré sur 0, apparait
G. Durée tempête :
Paramétrable de 0 minutes à 120 minutes
H. Puissance tempête :
Paramétrable de 0% à 100%
Toutes les pompes de brassage auront cette puissance durant les tempêtes
I. Accalmie nocturne et alimentation :
Paramétrable de 0% à -100%
Toutes les pompes de brassage auront cette puissance durant les tempêtes et le nourrissage
J. Enregistrer :
Enregistre tous les paramètres (y compris l’état dans bouton de la page d’accueil) puis revient sur la page paramétrages.
K. Vers page paramétrages (sans sauvegarde)

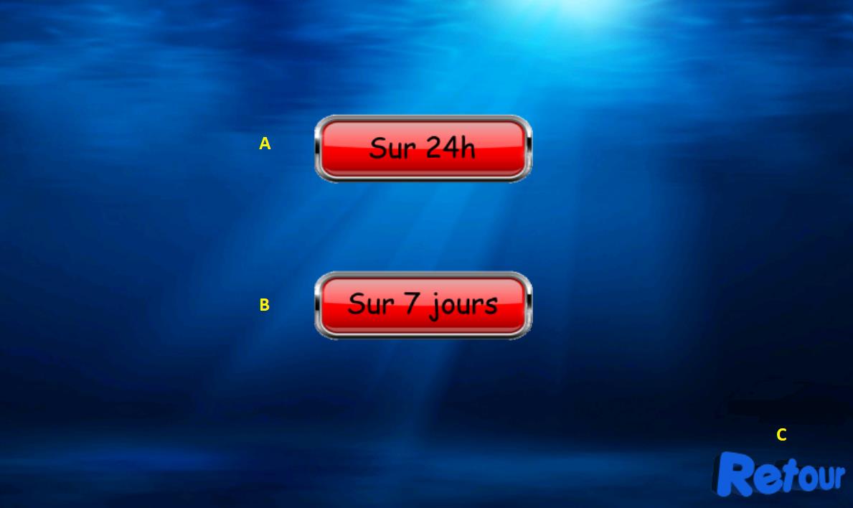
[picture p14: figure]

Page 18 sur 39

### 5.Page choix du graphique

A. Vers la page graphique sur 24H
B. Vers la page graphique sur 7 jours
C. Retour vers la page MENU

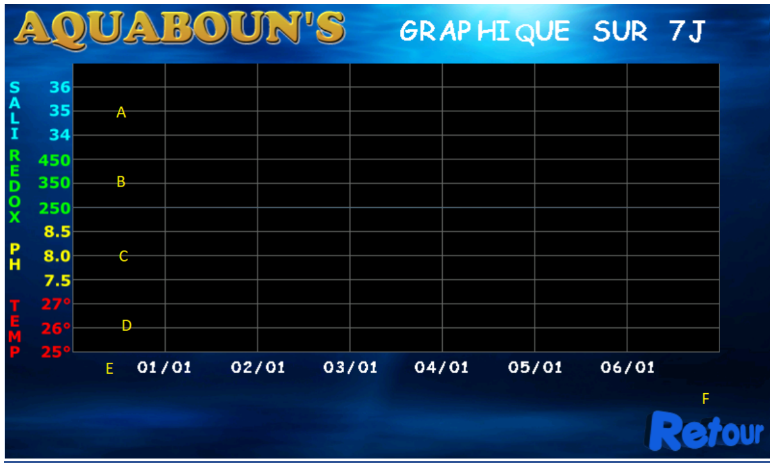
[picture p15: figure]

Page 19 sur 39

### 6.Page graphique 24H ou 7 jours :

A. Courbe de la salinité (non disponible pour les écrans standard)
B. Courbe du Redox (non disponible pour les écrans standard)
C. Courbe du Ph
D. Courbe de la température
E. Indique la date des mesures
F. Retour vers la page choix du graphique

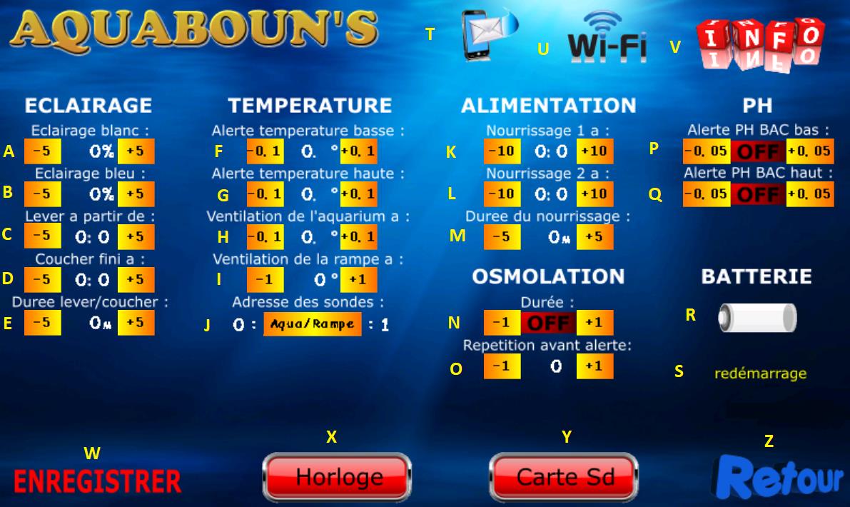
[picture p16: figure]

Page 20 sur 39

### 7.Page paramétrage :

A. Eclairage Blanc :
Puissance max du canal blanc**
Paramétrable de 0% a 100% par tranche de 5%.
B. Eclairage Bleu :
Puissance max du canal bleu**
Paramétrable de 0% à 100% par tranche de 5%.
C. Lever à partir de :
Heure du début du lever
Paramétrable de 0H00 à (coucher-(2xduree)) par tranche de 5 minutes.
Exemple, si coucher = 20h00 et durée = 60min, lever peut-être paramétré de 0h00 à 18h00 (20h-(2*60min)).
Si vous essayez de dépasser la limite, lever, coucher et durée : clignoteront en rouge sans prendre en compte le changement.
D. Coucher fini a :
Heure de fin du coucher
Paramétrable de (lever+(2xduree)) à 0h00 par tranche de 5 minutes.
Exemple, si lever = 10h00 et durée = 60min, coucher peut-être paramétré de 12h00 (10h+ (2*60min)) à 0h00.
Si vous essayez de dépasser la limite, lever, coucher et durée : clignoteront en rouge sans prendre en compte le changement.

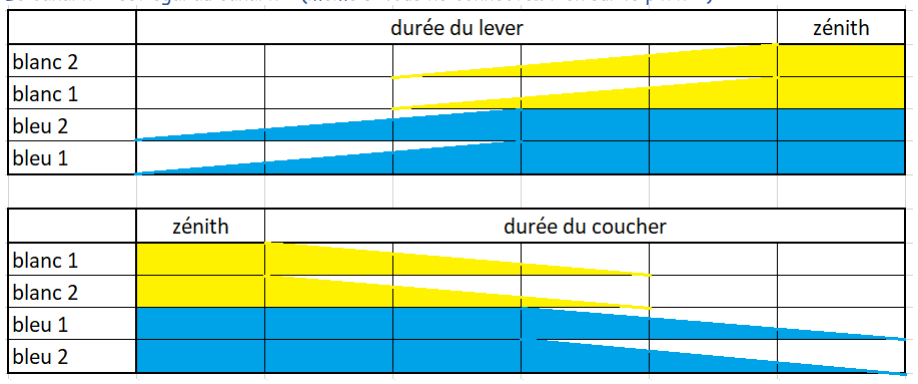
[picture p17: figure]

Page 21 sur 39

E. Durée lever / coucher :
Paramétrable de 0 minutes à la moitié de la durée du zénith, par tranche de 5minutes.
Exemple, si lever = 10h00 et coucher 20h00, durée peut être paramétrée de 0 minute à 300 minutes ((20h00-10h00) /2).
Si vous essayez de dépasser la limite, lever, coucher et durée : clignoteront en rouge sans prendre en compte le changement.
Voici la courbe de progression lors du lever et coucher « standard » 4 canaux, 2 bleus + 2 blancs :

Voici la courbe de progression si vous paramétrez dans config.h un seul canal blanc et bleu Le canal n°2 est égal au canal n°1 (même si vous ne connectez rien sur le pin n°2)

Vous pouvez aussi paramétrer 1 couleur en 1 canal et l’autre en 2 si besoin.

F. Alerte température basse :
Signal sonore + SMS si la température mesurée atteint la température basse paramétrée.
Paramétrable de 18° a (alerte température haute – 1°)
Si vous essayez de dépasser la limite, alerte température basse et alerte température haute : clignoteront en rouge sans prendre en compte le changement.

Page 22 sur 39

G. Alerte température haute :
Signal sonore + SMS si la température mesurée atteint la température haute paramétrée.
Paramétrable de (alerte température basse + 1°)
Si vous essayez de dépasser la limite, alerte température basse et alerte température haute : clignoteront en rouge sans prendre en compte le changement.

Volontairement l’AQUABOUNS n’est pas conçu pour réguler la température de l’aquarium mais pour mesurer et sécuriser la température en cas de dérive.

H. Ventilation de l’aquarium :
Température de déclenchement des ventilateurs de l’aquarium
Arrêt de la ventilation lorsque la température a atteint (ventilation de l’aquarium – 0.3°)
Paramétrable de (alerte température basse + 0.5°) à (alerte température haute - 0.5°)
Si vous essayez de dépasser la limite, alerte température basse et alerte température haute : clignoteront en rouge sans prendre en compte le changement.
I. Ventilation de la rampe :
Température de déclanchement des ventilateurs de la rampe.
Arrêt de la ventilation lorsque la température a atteint (ventilation de la rampe -0.3°)
Paramétrable de 0° à 100°
Si vous essayez de dépasser la limite, ventilation de la rampe clignotera en rouge sans prendre en compte le changement.
J. Adresse des sondes de température :
Inverse l’adresse des sondes, adresse 0 = aquarium / rampe = adresse 1 OU adresse 0 = rampe / sonde = adresse 1
K. Nourrissage 1 :
Heure de déclanchement du nourrissage automatique 1.
Paramétrable de 0h00 à 23h50
Si vous essayez de dépasser la limite, nourrissage clignotera en rouge sans prendre en compte le changement.
L. Nourrissage 2 :
Heure de déclanchement du nourrissage automatique 2.
Paramétrable de 0h00 à 23h50.
Si vous essayez de dépasser la limite, nourrissage clignotera en rouge sans prendre en compte le changement.

Page 23 sur 39

M. Durée du nourrissage :
Pendant cette durée, la pompe de remonté est arrêtée (si paramétré en Delay) et le brassage est réduit (si paramétré)
Paramétrable de 0 minute à 120 minutes
Si vous essayez de dépasser la limite, durée du nourrissage clignotera en rouge sans prendre en compte le changement.
N. Durée osmolation :
Durée max d’osmolation, si le flotteur de niveau constant est toujours en position bas à la fin de cette durée, l’osmolation marque un temps de pause et incrémente un compteur (voir paragraphe O) Paramétrable de 0 seconde à 60 secondes.
Si vous essayez de dépasser la limite, durée osmolation clignotera en rouge sans prendre en compte le changement.
O. Répétition avant alerte :
Nombre de fois ou l’osmolation se déclenche en continu durant toute la durée paramétrée (voir paragraphe
N) avant de déclencher une alerte.
Signal sonore + SMS + coupure de l’osmolation si le nombre de répétition est atteint.
Paramétrable de 1 seconde à 20.
Si vous essayez de dépasser la limite, répétition avant alerte clignotera en rouge sans prendre en compte le changement.
P. Alerte PH BAC bas :
Signal sonore + SMS + coupure du CO2 si le Ph de l’aquarium atteint alerte Ph bac bas.
Paramétrable de Ph 5.00 à (alerte ph bac haut – 0.05)
Si le paramétrage atteint alerte Ph bac haut, alerte Ph bas et haut passeront en
Si vous essayez de dépasser la limite basse, alerte ph bac bas clignotera en rouge sans prendre en compte le changement.
Q. Alerte PH BAC haut :
Signal sonore + SMS si le Ph de l’aquarium atteint alerte Ph bac haut.
Paramétrable de (alerte ph bac bas + 0.05) à Ph 9.00
Si le paramétrage atteint alerte Ph bac bas, alerte Ph bas et haut passeront en
Si vous essayez de dépasser la limite haute, alerte ph bac haut clignotera en rouge sans prendre en compte le changement.
R. Niveau batterie :
Indique le niveau de charge de la batterie de secours si une batterie est branchée.
S. Redémarrage manuel
Pour redémarrer manuellement l’AQUABOUNS

Page 24 sur 39

T. Vers la page paramétrage SMS
U. Vers la page paramétrage WIFI
V. Vers la page INFO
W. Enregistrer :
Enregistre tout les paramètres (y compris l’état dans bouton de la page d’accueil) puis revient sur la page d’accueil.
X. Vers la page paramétrage de l’horloge
Y. Vers la page de visualisation des évènements
Z. Vers page d’accueil (sans sauvegarde)

Page 25 sur 39

### 8.Page GSM

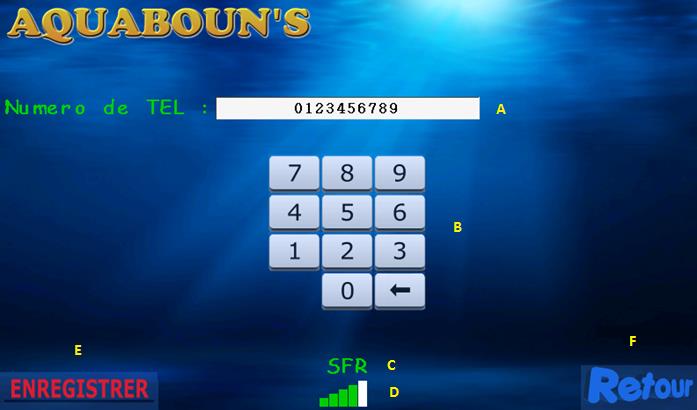
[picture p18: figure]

A. Numéro de téléphone :
Indique le numéro de téléphone paramétré à l’ouverture de la page.
B. Clavier :
Pour saisir modifier le numéro de téléphone
C. Indique le statut du Gsm :
Si le Gsm est connecté au réseau, affiche le nom de l’opérateur. Si non connecté au réseau, indique :
Si le module n’est pas détecté, indique :
D. Puissance signal :
Si le module est connecté au réseau, indique la puissance du signal.
E. Enregistrer :
Enregistre le numéro de téléphone puis revient sur la page paramétrage.
F. Vers page paramétrage (sans sauvegarde)

Page 26 sur 39

### 9.Page WIFI

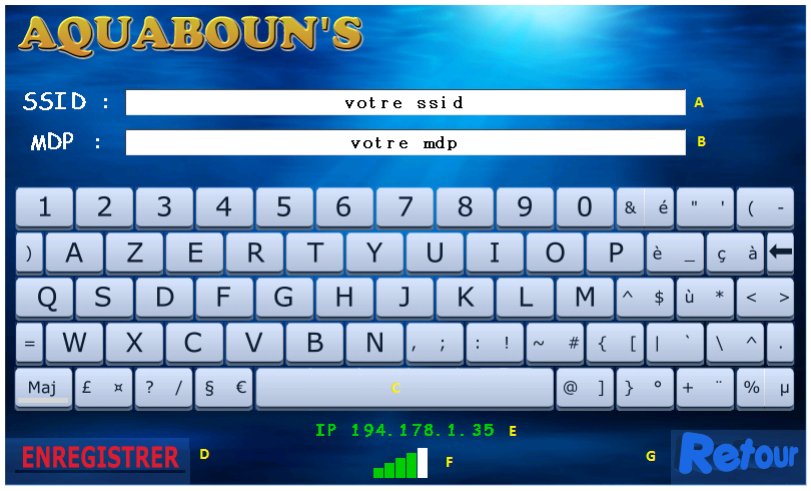
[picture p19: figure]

A. SSID :
Indique le SSID paramétré à l’ouverture de la page.
Pour modifier le SSID il faut toucher les champs puis saisir.
B. Mots de passe :
Indique le Mot de passe paramétré à l’ouverture de la page.
Pour modifier le Mot de passe il faut toucher les champs puis saisir.
C. Clavier :
Pour modifier le SSID ou Mot de passe
D. Enregistrer :
Enregistre le SSID et Mot de passe puis revient sur la page paramétrages.
E. Indique le statut du WIFI :
Si le module est connecté au réseau, affiche l’adresse IP >>> Sa LED est allumée
Si non connecté au réseau, indique : | >>> La LED du module Wifi est éteinte
Si le module n’est pas détecté, indique : | >>> Sa LED est éteinte
F. Puissance signal :
Si le module est connecté au réseau, indique la puissance du signal.
G. Vers page paramétrages (sans sauvegarde)

Page 27 sur 39

### 10. Page Horloge

A. Heure :
Paramètre l’heure
B. Date :
Paramètre la date
C. Relance Alertes :
Paramétrable de 0h à 23h.
Durant cette période l’alarme sonore est activée et les alertes par SMS sont relancées toutes les heures en cas d’anomalies.
D. Enregistrer :
Enregistre tous les paramètres (y compris l’état dans bouton de la page d’accueil) puis revient sur la page paramétrages.
E. Vers page paramétrages (sans sauvegarde)

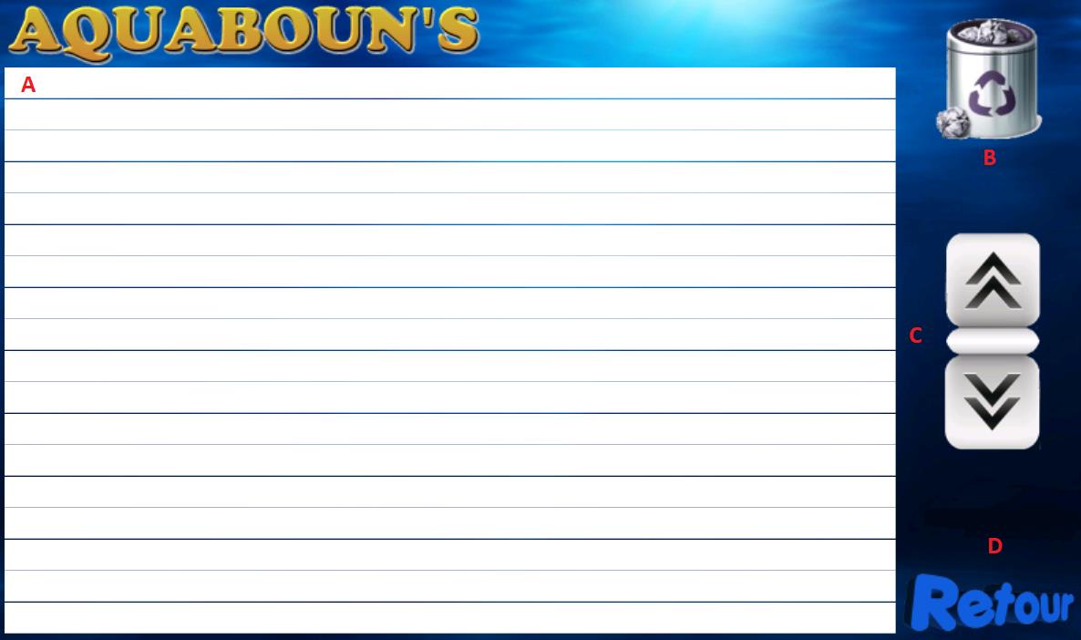
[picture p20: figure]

Page 28 sur 39

### 11. Page SD

A. Indique les évènements survenus :
B. Efface tous les évènements
C. Fait défiler les évènements
D. Retour vers la page paramétrage

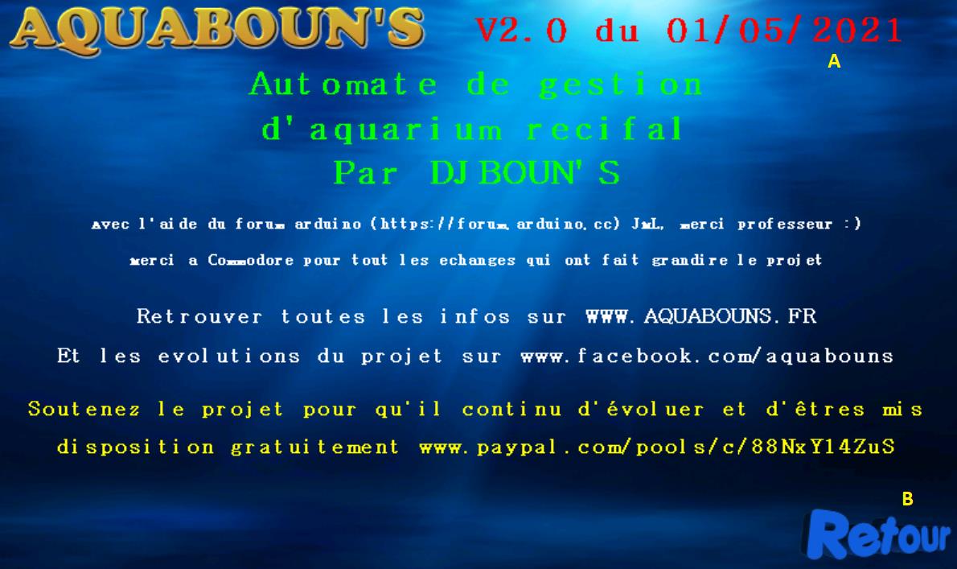
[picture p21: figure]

Page 29 sur 39

### 12. Page INFO

A. Version :
Version actuelle de l’automate
B. Vers page paramétrages (sans sauvegarde)

Page 30 sur 39

### 13. Fonctions en arrière-plan :

A. Rétroéclairage de l’écran :
Si l’écran est sur la page d’accueil, le rétroéclairage se coupera automatiquement au bout d’une minute. Il suffit de le toucher pour le rallumer.
B. Flotteurs :
1> Si le flotteur de la réserve Vide est activé, l’osmolation est coupée au bout de 5 secondes, un signal sonore retenti et un SMS est envoyé. Si le flotteur repasse en position haute plus de 15 minutes d’affilé, l’osmolation est réactivée.
2> Si le flotteur du godet plein est activé, l’écumeur est coupé, un signal sonore retenti et un SMS est envoyé.
3> Si le flotteur Niveau écumeur est activé, l’écumeur est coupé.
4> Si le flotteur d’osmolation est toujours actif alors que le compteur est atteint, l’osmolation est coupée, un signal sonore retenti et un SMS est envoyé.
5> Si le flotteur sécurité décante est activé, l’osmolation est coupée, l’écumeur est coupé, un signal sonore retenti et un SMS est envoyé. Quand le flotteur repasse en position basse, un SMS est envoyé, l’osmolation et l’écumeur son réactivés.
C. Chauffage :
La gestion de la température est à faire via un thermostat externe (exemple, thermoplongeur régulé) Le programme sécurise la température en cas de défaillance de votre chauffage en coupant son alimentation dès que celle-ci est égale ou supérieure à la température de ventilation et vous alertes par SMS en cas de température trop haute ou trop basse.
D. SMS, signal sonore, sauvegarde sur SD :
Un signal sonore retenti et un SMS est envoyé lorsqu’une des anomalies suivantes est détectée :
- Si Température du bac trop basse ou trop haute (SMS au retour à la normale)
- Si Ph du bac trop bas ou trop haut (SMS au retour à la normale)
- Si Compteur osmolation atteint
- Si Coupure EDF (si alimentation de secours) (SMS au retour à la normale)
- Si réserve d’eau vide
- Si flotteurs sécurité décante en position haute
- Si godet écumeur plein
Quand l’Arduino démarre, lorsque le GSM ou WIFI reboot ou si l’une de ces erreurs se produisent, l’info seras enregistrée sur la carte SD dans le fichier erreur.txt
E. GSM :
Si le module Gsm venait à ne plus répondre, l’Arduino le reboot automatique.

Page 31 sur 39

F. Wifi :
Si le module Wifi venait à ne plus répondre, l’Arduino le reboot automatique.
Si le module Wifi venait à « bugger » (pendant plus de 8 secondes), Il se reboot puis demande les identifiants de connexion automatiquement à l’Arduino.
La LED bleu sur le module s’allume quand la connexion Wifi est établie.
La LED bleu sur le module s’éteint quand la connexion Wifi n’est pas faite.
G. Arduino :
Si l’Arduino venait à ne plus répondre (pendant plus de 8 secondes), Il se reboot automatiquement. Un message de redémarrage est inscrit sur la carte SD

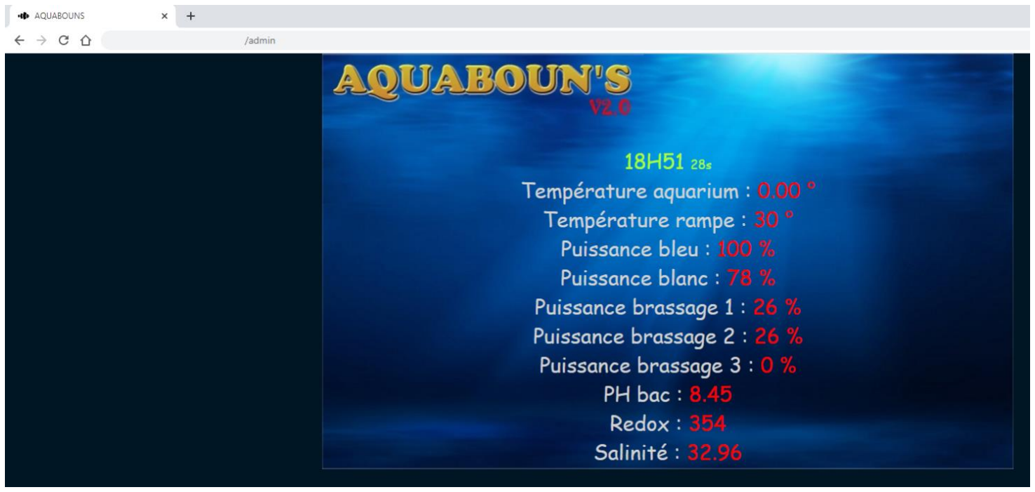
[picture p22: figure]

Page 32 sur 39

### 14. Page WEB

a) Accéder à la page web en local (de chez vous, à partir d’un appareil connecté au même réseau Wifi que votre module) :
Il vous suffit de taper dans votre navigateur ne numéro d’IP affiché sur la page Wifi.

La page web est automatiquement rafraichis toute es 10 secondes.

b) Accéder à la page web à distance :
Il vous faut paramétrer la redirection des ports de votre box. Chaque box étant différentes, Je ne peux que vous montrez la procédure Pour 2 box différentes.
N’hésitez pas à me fournir vos exemples pour votre matériel

Page 33 sur 39

### Exemple pour une Box BOUYGUES :

1. Dans votre navigateur vous taper : http://192.168.1.254 , puis votre code ADMIN. Lors de cette procédure, votre module Wifi doit être connecté au réseau.
2. Dans la partie Wifi, votre module Wifi doit apparaitre sous un nom genre ESP ***
Vous pouvez vérifier qu’il s’agit bien du module en cliquant sur les trois points puis informations détaillées, le numéro d’IP doit correspondre à l’IP présent sur la page Wifi.
Pour plus de simplicité, renommer cet appareil « AQUABOUNS »

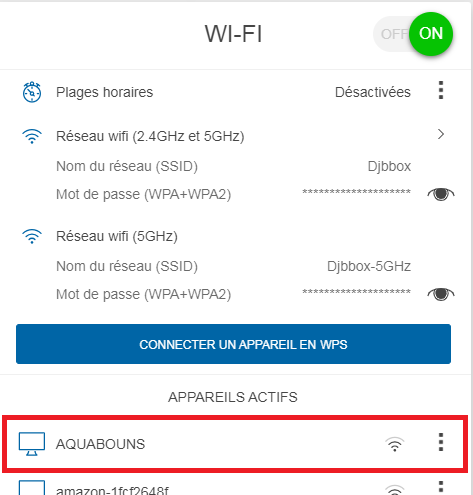
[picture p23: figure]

3. Allez dans BBOX
4. Dépliez SERVICES DE LA BOX
5. Rentrez dans DHCP
6. En bas de la page allez dans ATRIBUER UNE ADRESSE STATIQUE
7. Mettez-en ON
8. Ajoutez un équipement

Equipement = sélectionnez votre module Wifi (qui doit s’appeler AQUABOUNS à présent) Adresse IP statique = adresse IP de la page Wifi
Adresse MAC = ne pas toucher
Nom de l’équipement = AQUABOUNS

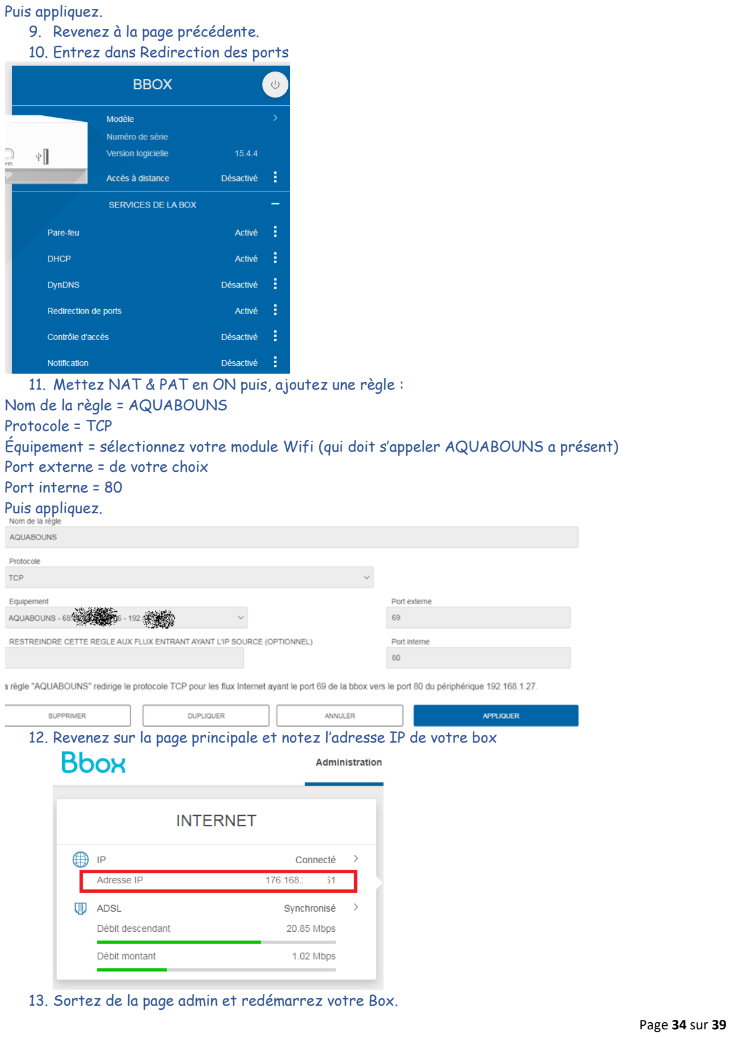
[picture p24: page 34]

Page 34 sur 39

Puis appliquez.
9. Revenez à la page précédente.
10. Entrez dans Redirection des ports
11. Mettez NAT & PAT en ON puis, ajoutez une règle :
Nom de la règle = AQUABOUNS
Protocole = TCP
Équipement = sélectionnez votre module Wifi (qui doit s’appeler AQUABOUNS a présent) Port externe = de votre choix
Port interne = 80
Puis appliquez.
12. Revenez sur la page principale et notez l’adresse IP de votre box
13. Sortez de la page admin et redémarrez votre Box.

### Exemple pour une Freebox Crystal :


Page 35 sur 39

(Merci Commodore (http://www.recifal-france.fr/membre7869.html) pour m’avoir partagé cette partie)

1. Se loger sur https://subscribe.free.fr/login/
2. Sélectionnez afficher mon adresse IP

Page 36 sur 39

3. Ouvrez une autre fenêtre dans le navigateur et tapez votre adresse dans le champ URL
4. Cliquez sur Format texte
5. Localisez l’adresse IP de votre ESP et recopier son adresse MAC


Page 37 sur 39

6. Revenez sur la configuration de votre box et sélectionnez cette fois « Paramétrer mon routeur »
7. Cliquez sur Redirections/ Baux DHCP
8. entez dans l’ordre :
- 1 : 69
- 2 : 51 (L’adresse IP n’est pas comprise dans la plage du DHCP (1-50 pour moi)
- 3 : 80
- 4 : Ajouter
- Resultat dans le 5
- Pour le DHCP permanent :
- 6 : 51 (L’adresse IP n’est pas comprise dans la plage du DHCP (1-50 pour moi)
- 7 : adresse MAC de l’ESP
- 8 : cliquer sur Ajouter
- Résultat dans le 9
- 10 : Sauvegarder les paramètres

Page 38 sur 39

9. Redémarrez votre box
10. Redémarrez l’Aquabouns
11. L’adresse IP de l’Aquabouns est passée à 192.168.*.* (ce que vous avez mis)
12. Prenez votre navigateur et tapez votre adresse IP xx.xx.xx.xx:69 dans le champ URL et si tout se passe bien la page d’accueil de l’Aquabouns s’affichera.
13. Pour la REVERSE DNS indiquer juste un nom dans « Entrée DNS personnalisée ».
14. Quelques heures plus tard au lieu de votre IP : 69 vous tapez dans la barre d’URL LeNomDonne.hd.free.fr:69
15. Une fois la Box redémarrée et le module Wifi reconnecté, allez dans un navigateur et tapez l’adresse IP de votre Box suivi du port externe que vous avez attribué à l’étape 11, exemple : si adresse Box = 176.168.123.456 et port externe 69, tapez 176.168.123.456 :69
La page doit apparaitre de n’importe où à partir du moment où vous avez une connexion internet.

# III. A bientôt :

## Si le montage n’est pas à votre porté :


Page 39 sur 39

Profiter bien de cet automate gratuit et venez partager vos impressions, vos expériences, vos remarques, vos idées sur le groupe FACEBOOK https://www.facebook.com/groups/aquabouns/

N’hésitez pas à me contacter : www.facebook.com/aquabouns ou contact@aquabouns.fr

## Je réalise des SHIELD pour Arduino Méga spécialement conçu pour l’Aquabouns :

# www.pcbouns.fr

## SI le projet vous plait et que vous souhaitez qu’il perdure, évolue et continu d’être mis à disposition GRATUITEMENT, pensez à FAIRE UN DON

## https://paypal.me/ProjetAquabouns

## AQUABOUN’S V2.0 par DJBOUNS

2021

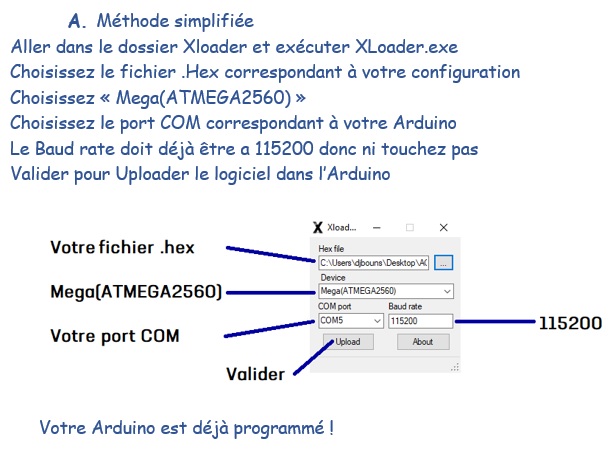
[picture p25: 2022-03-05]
Notices & Co/Notices/instalation simplifiée Aquabouns V3.jpg

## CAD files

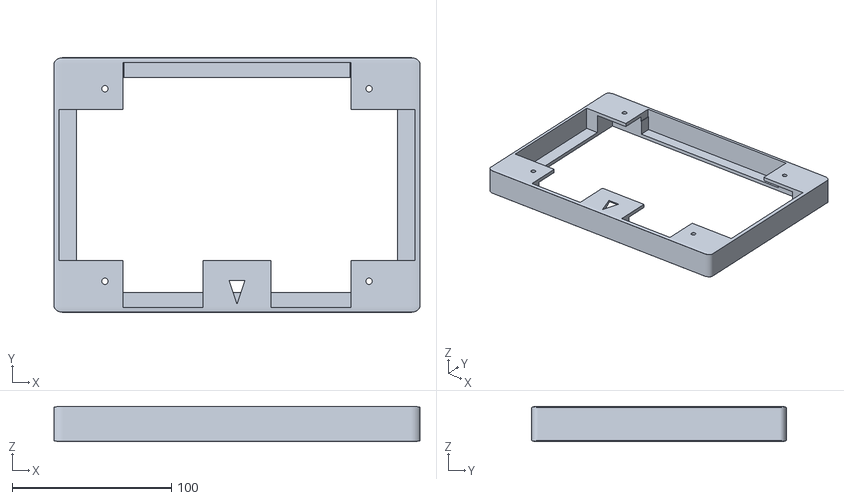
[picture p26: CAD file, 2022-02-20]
Notices & Co/3D/cadre 7.0 enhanced capacitif.stl
230.0 x 160.0 x 22.0

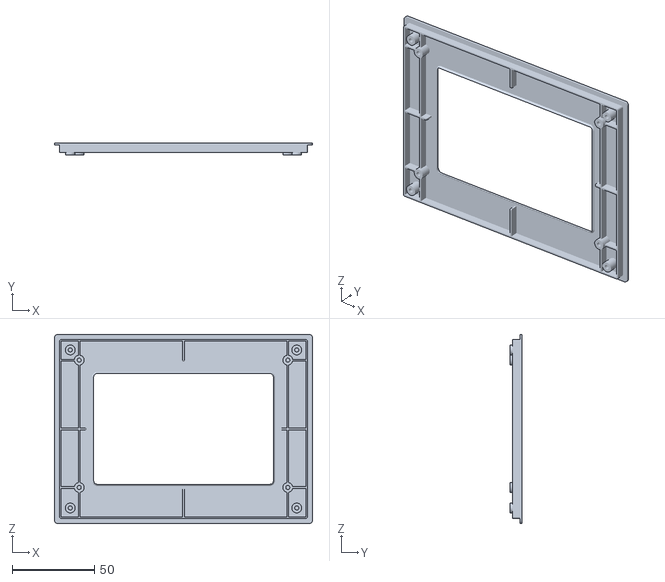
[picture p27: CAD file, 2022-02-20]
Notices & Co/3D/cadre 5.0 V2.stl
157.2 x 7.50 x 115.2

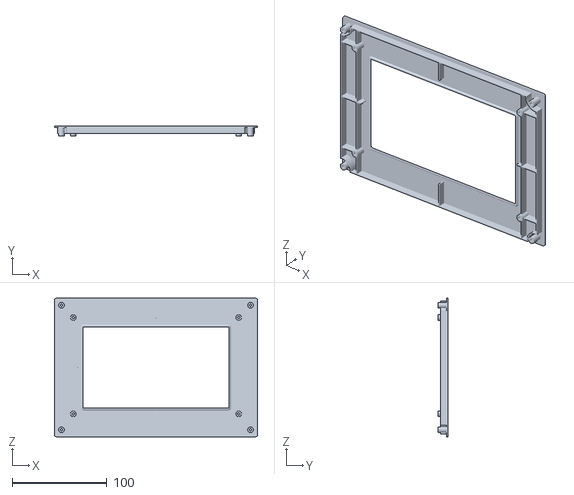
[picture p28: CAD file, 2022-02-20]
Notices & Co/3D/cadre 7.0 V2.stl
214.2 x 10.1 x 146.2

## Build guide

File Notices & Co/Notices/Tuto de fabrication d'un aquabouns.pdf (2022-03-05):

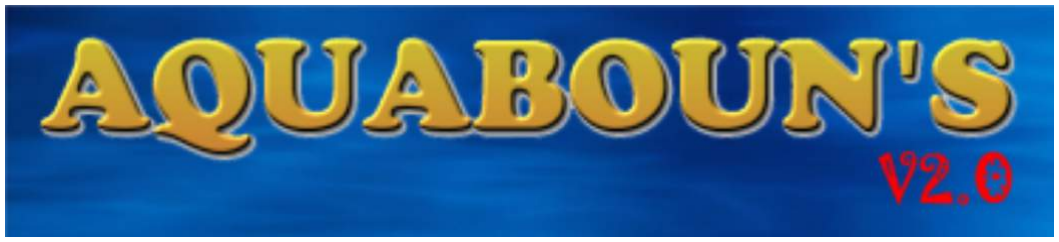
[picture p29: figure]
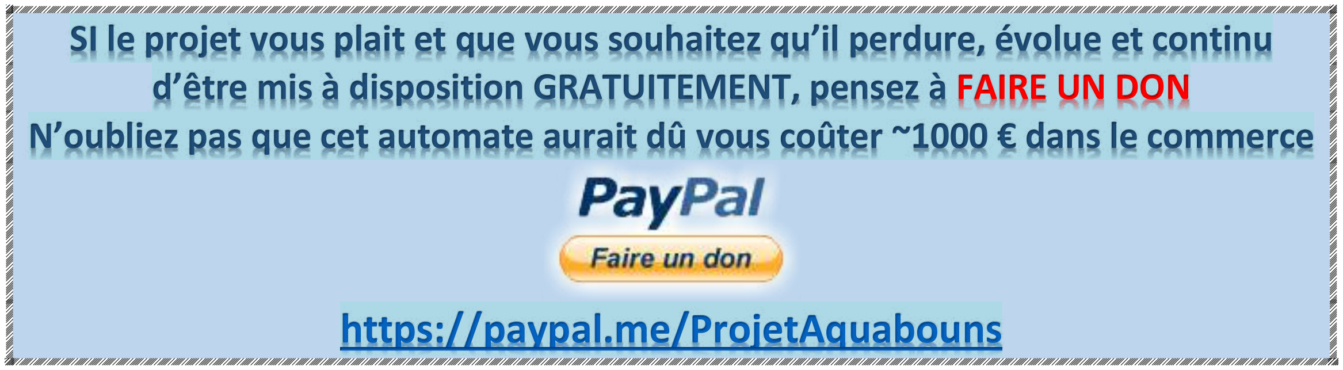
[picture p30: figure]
https://paypal.me/ProjetAquabouns

Page 1 sur 27

# Automate de gestion d’aquarium récifal

## Par DJBOUNS

MAJ 03/09/21

Bonjour,

Ce projet a débuté en Mai 2017 dans l’intention de réaliser un automate pour aquarium récifal complet, fiable et à faible coût pour qu’un maximum de récifalistes puissent en profiter.

Il verra le jour grâce à quelques rares personnes qui m’ont aidé ou guidé quand j’en avais besoin.
Un GRAND merci à JML du forum Arduino pour son aide et tous ses conseils reçus, qui ont permis à ce projet d’être aussi abouti.
Merci à tous le forum Arduino pour son aide.
Merci à Commodore pour sa participation dans le développement de cette V2.0

AQUABOUN’S représente des milliers d'heures de travail pour ~6000 lignes de code, 1000 lignes de plus que la V1.0.
Cela représente également des dépenses importantes pour tester et trouver le matériel le plus adapté. Il est mis à disposition entièrement gratuitement afin que tout le monde puisse profiter d’un automate à faible coût.
Vous pouvez le télécharger à partir du site : WWW.AQUABOUNS.FR

N’hésitez pas à me faire part de toute amélioration ou évolution souhaitées : www.aquabouns.fr ou www.facebook.com/aquabouns ou aquabouns@hotmail.com ou sur le groupe https://www.facebook.com/groups/aquabouns/

### SI le projet vous plait et que vous souhaitez qu’il perdure, évolue et continu d’être mis à disposition GRATUITEMENT, pensez à FAIRE UN DON N’oubliez pas que cet automate aurait dû vous coûter ~1000 € dans le commerce

### Merci et bon montage à tous

Page 2 sur 27

# SOMMAIRE

I. Composants nécessaires | Page 3
II. Affectation des pins de l’Arduino | Page 6

### III. Composant connectés aux Pins | Page 7

1. DS3231 + MODUL ATLAS | Page 7
2. Carte SD | Page 10
3. pinInCoupureCourant | Page 10
4. pinInBatterie | Page 10
5. Gsm + hardResetGSM | Page 11
6. Nextion | Page 12
7. d1mini + hardResetWIFI | Page 13
8. pinOutBrassage 1, 2 et 3 | Page 14
9. pinOUTOscillo 1, 2 et 3 | Page 16
10. pinOutEclairage 1, 2, 3 et 4 | Page 16
11. pinOutbuzzer | Page 17
12. pinOutRelais***** | Page 18
13. pinInSondeDs18b20 | Page 20
14. pinInFlotteur***** | Page 22
15. pinOutRelaisDistributeurNouriture | Page 22
16. pinOutBatterie | Page 26
IV. A bientôt | Page 27

Page 3 sur 27

## !!! ATTENTION !!!

Je ne suis pas électricien ni électronicien.
Ce qui suit n’est qu’un simple partage d’expérience. Toutes connexions/interfaces avec des tensions dangereuses ne doivent se faire que par du personnel qualifié et selon les normes en vigueur afin d’éviter tout risque d’accident ou d’incendie.
Ne pas laisser sans surveillance. Djbouns décline toute responsabilité quant aux dommages directs ou indirects qui pourraient être causés.

### I. Composants :

Vous pouvez réaliser le montage avec les composants de votre choix.
À titre indicatif, en Orange, le tarif constaté des composants chez des vendeurs en France sans les frais de port, www.amazon.fr, www.ebay.fr, https://store.arduino.cc,https://www.itead.cc/display/nextion.html , https://atlas-scientific.com
- 1 Arduino Méga (officiel 35€, copie 15€)
- 1 alimentation 5V mini 3A (15€)
- 3 Modules Atlas Scientifique (pour le PH, Redox, Salinité) (de 30€ à 50€ pcs sans les sondes) Pour des mesures fiables il est recommandé de les associer à une alimentation isolée (15€ pcs)
- 1 module GSM compatible commande AT (type sim800l) (15€)
- 1 module WIFI Wemos d1 mini (10€)
- 1 lecteur SD (5€)
- 1 horloge ds3231 (6€)
- 2 sondes de température ds18b20 (pour le Bac et pour la rampe) (6€ pcs)
- 5 flotteurs (niv constant, niv réserve, niv écumeur, godet écumeur, niv sécurité) (3€ pcs)
- 4 relais (carte 8 relais « Arduino » 8€, relais DIN pour tableau 45€)
- 1 écran NEXTION, Vous avez la possibilité d'utiliser plusieurs modèles d'écran NEXTION du moment que la résolution est 800*480 (IMPORTANT, voir détail plus bas) (56€ - 93€)
- 1 Batterie et son système de charge (nécessaire pour être alerté en cas de coupure EDF) (40€)

### !!! L’Aquabouns est UPGRADABLE !!!

Les composants pour l’utiliser a minima sont une alimentation, l’Arduino, l’écran, l’horloge.
Avec cette configuration minimaliste, vous pourrez déjà contrôler l’éclairage, le brassage, les oscillateurs. À vous d’ajouter ou non d’autres périphériques pour bénéficier de leurs fonctions.
Cela est valable également pour les modules Atlas, vous pouvez ajouter un module de votre choix, ou une combinaison de deux modules différents ou les 3 pour bénéficier des trois mesures.

### TOTAL entre ~95€ et ~450€

(Sans les sondes)
La qualité et le prix des sondes (ph, orp, conductivité) varies tellement qu’elles n’ont pas été pris en compte pour le calcul

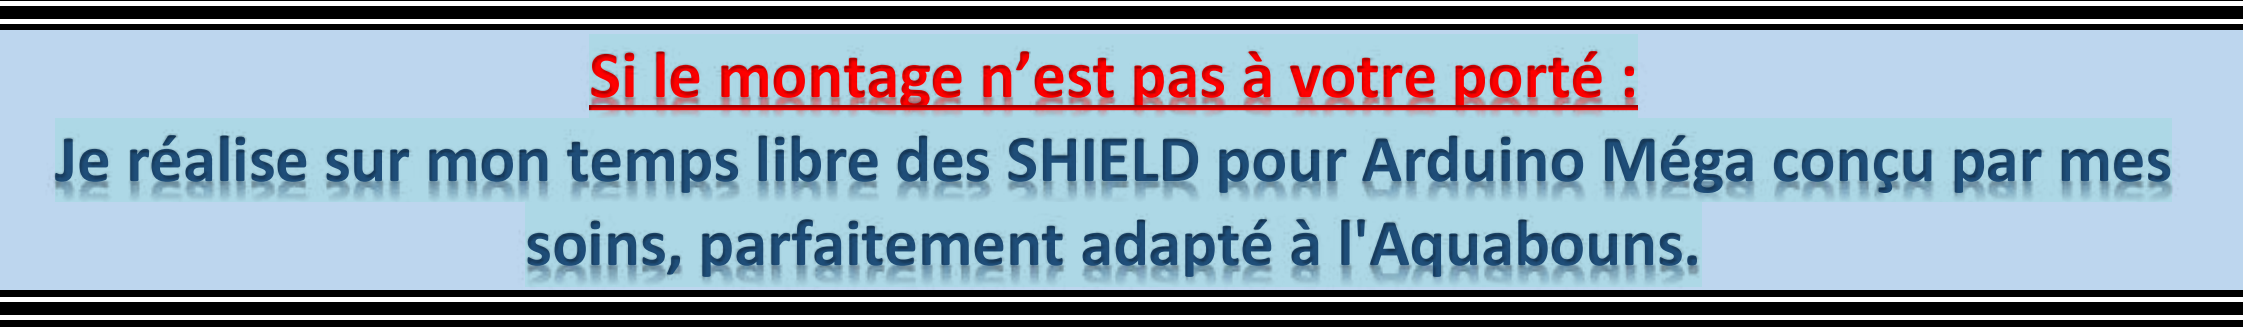
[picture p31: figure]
Si le montage n’est pas à votre porté :
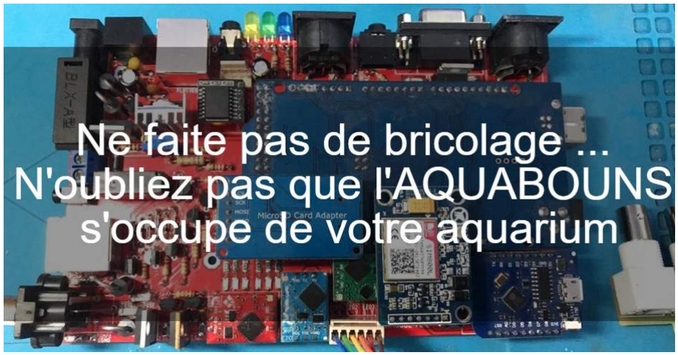
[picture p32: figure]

Page 4 sur 27

### !!! IMPORTANT !!!

N’oubliez pas que pour réaliser un montage, il vous faudra ajouter à ces prix indicatifs les frais de port, un boitier, le câblage, toutes les connexions et périphériques éventuels (oscillateur, pompe osmolation, ventilateurs, etc…), et divers fournitures et composants électroniques. Dans certain cas, vous pourriez même avoir à payer le dédouanement (20% TVA + frais de traitement)

Tenez compte du coût de tout ce matériel afin de réaliser un montage fiable et de qualité

### Je réalise sur mon temps libre des SHIELD pour Arduino Méga conçu par mes

soins, parfaitement adapté à l'Aquabouns.

N’hésitez pas à me contacter : www.aquabouns.fr ou www.facebook.com/aquabouns ou aquabouns@hotmail.com

Page 5 sur 27

### !!! TRES IMPORTANT !!!

### Il faut impérativement utiliser un écran NEXTION ORIGINAL, les copies ne

reconnaissent pas le fichier contenant le logiciel.

### https://nextion.itead.cc/nextion-shop/

Afin de faire votre choix il faut évaluer vos besoins : taille 5" ou 7", version standard ou améliorée (processeur plus puissant, nu ou avec boitier selon le montage que vous souhaitez)

>>> Le principe de l'écran tactile résistif : deux couches en surfaces séparées par de minuscules entretoises et parcourues de connecteurs.
Le toucher du doigt ou d'une pointe quelconque déforme la surface supérieure et met en contact ses connecteurs avec ceux de la surface intérieure. L'utilisation d'un stylet est souvent nécessaire.

>>> Le principe de l'écran tactile capacitif : Quand le doigt, conducteur d'électricité, touche l'écran, des charges électriques lui sont transférées. (Comme les smartphones en ce moment)

Les modèles compatibles :
Écran 5" NX8048T050_011R <<< version standard résistif nue
Écran 5" NX8048K050_011R <<< version améliorée résistif nue
Écran 7" NX8048T070_011R <<< version standard résistif nue
Écran 7" NX8048K070_011R <<< version améliorée résistif nue
Écran 7" NX8048K070_011C <<< version améliorée capacitif avec boitier

!!! IMPORTANT !!!
Les écrans « standards » ne pourront afficher que les courbes PH + Température Les écrans « améliorées » afficheront les courbes PH + Température + Redox + Salinité

Page 6 sur 27

### II. Affectation des pins de l’Arduino :

Vous avez la possibilité de connecter vos peripheriques sur les Pins de l’arduino de votre choix en respectant les restrictions suivantes ( la même affectation doit être faite dans le logiciel) :

Obligatoire sur ces Entrées/sorties :
PIN 20 sda > ds3231 + MODUL ATLAS
PIN 21 scl > ds3231 + MODUL ATLAS
PIN 50 miso > carte sd
PIN 51 mosi > carte sd
PIN 52 sck > carte sd
PIN 53 cs > carte sd

Sur les Entrées/sorties analogiques de votre choix : pinInCoupureCourant
pinInBatterie

Sur les Entrées/sorties séries de votre choix : d1mini
gsm
nextion

Sur les Entrées/sorties digitales PWM de 2 à 13 et 44 a 46 : pinOutBrassage 1, 2 et 3
pinOUTOscillo 1, 2 et 3
pinOutEclairage 1, 2, 3 et 4
pinOutbuzzer

Sur les Entrées/sorties restantes de votre choix : pinOutRelaisRemontee
pinOutRelaisChauffage
pinOutRelaisEcumeur
hardResetGSM
hardResetWIFI
pinInSondeDs18b20
pinInFlotteurGodetEcumeur
pinInFlotteurReserve
pinInFlotteurDispo
pinInFlotteurReserveHaut
pinInFlotteurOsmolation
pinInFlotteurNiveauEcumeur pinOutRelaisDistributeurNouriture pinInFlotteurSecurite
pinOutBatterie
pinOutRelaisOsmolation
pinOutRelaisVentilateurBac pinOutRelaisVentilateurRampe

Page 7 sur 27

## III. Composants connectés aux Pins :

1. DS3231 (horloge) + MODUL ATLAS (mesures PH et/ou ORP et/ou EC)

Ø L’horloge est une pièce centrale de l’AQUABOUNS.
Des périphériques comme l’éclairage, le brassage, le nourrissage sont contrôlé en fonction de celle-ci. C’est pour cette raison que j’ai choisi d’utiliser une DS3231 plutôt qu’une DS1317 par exemple. Datasheet : https://datasheets.maximintegrated.com/en/ds/DS3231-DS3231S.pdf
Leur installation ne nécessite la connexion que de deux fils (SCL/SDA) en plus de l’alimentation.

Ø Il vous est aussi possible d’ajouter ou non 1, 2 ou 3 modules de prise de mesure Atlas Scientific : PH : https://atlas-scientific.com/embedded-solutions/ezo-ph-circuit/
ORP : https://atlas-scientific.com/embedded-solutions/ezo-orp-circuit/
EC : https://atlas-scientific.com/embedded-solutions/ezo-conductivity-circuit/
(Impossible d’installer 2 fois le même module)
Les modules communiquent eux aussi via les connexions SCL/SDA

Ø Important, le mode de communication par défaut des modules est UART. Avant de procéder à l’installation, il vous faut basculer les modules en mode de communication I2C en suivant les instructions suivantes pour tous les modules :
1) Retirer toute connexion au module
2) Relier TX a PGND
3) Alimenter le module > la LED doit devenir bleu

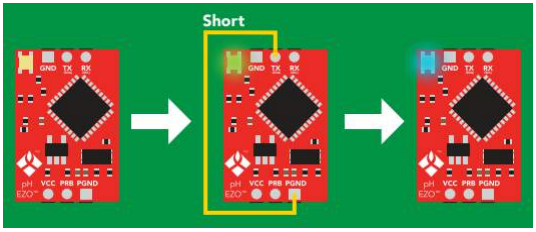
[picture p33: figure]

En fonction de votre installation, il sera peut-être nécessaire d’alimenter ces modules via des isolateurs https://atlas-scientific.com/ezo-accessories/basic-ezo-inline-voltage-isolator/

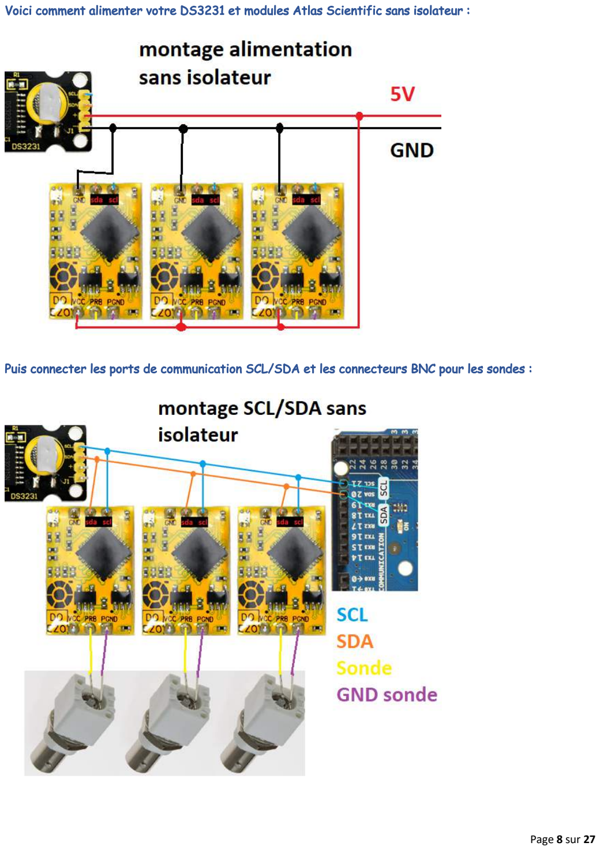
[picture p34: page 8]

Page 8 sur 27

Voici comment alimenter votre DS3231 et modules Atlas Scientific sans isolateur :

Puis connecter les ports de communication SCL/SDA et les connecteurs BNC pour les sondes :

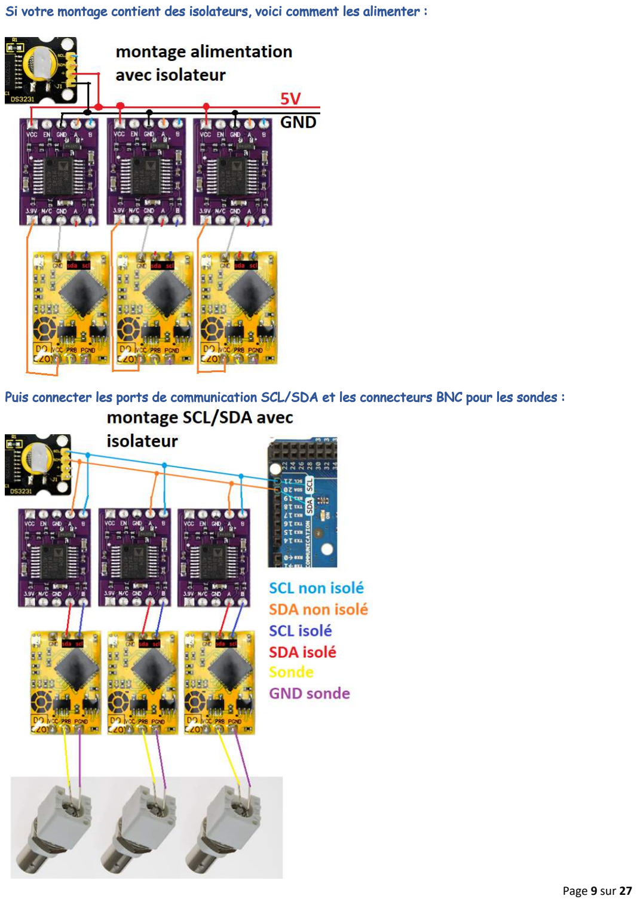
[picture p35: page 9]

Page 9 sur 27

Si votre montage contient des isolateurs, voici comment les alimenter :

Puis connecter les ports de communication SCL/SDA et les connecteurs BNC pour les sondes :

Page 10 sur 27

2. Carte SD

La carte SD permet de stocker diffèrent éléments comme votre SSID, votre numéro de téléphone, et même les mesures faites sur votre aquarium.
Il existe une multitude de modèle, le plus important étant de vérifier la tension de fonctionnement, 3.3V ou 5V.
Je préfère partir sur un modèle 5V alimenté par l’alimentation principale.
Exemple de connexion (vérifiez la correspondance des pins sur votre modèle) :
3. pinInCoupureCourant (entrée pour la présence alimentation)

Doit être relié à la source d’alimentation.
Il permet de détecter les coupures EDF et de vous prévenir si une alimentation de secourt est installé. Si vous n’avez pas de système d’alimentation de secours (batterie via pinInBatterie), ce Pin ne vous sera pas utile, reliez-le au 5V de l’Arduino.
Le programme reconnait la présence de l’alimentation quand le pin reçoit une tension supérieure à 2V, mais ATTENTION, l’Arduino supporte 5V MAX en entrée.
Selon la manière dont vous faite votre montage, il sera peut-être nécessaire de réaliser un pont diviseur de tension.
4. pinInBatterie (entrée pour connaitre la tension de la batterie de secourt)

Doit être relié à votre alimentation de secourt
Il permet de connaitre l’état de charge de votre batterie mais aussi de couper celle-ci quand la puissance devient trop faible afin de ne pas l’endommager.
Si vous n’avez pas de batterie de secourt, laisser ce pin libre.
Le programme a été configuré pour que la tension maximum de la batterie corresponde à une tension peu de 4.4V sur le pin de l’Arduino.
ATTENTION, l’Arduino supporte 5V MAX en entrée.
Selon la manière dont vous faite votre montage, il sera peut-être nécessaire de réaliser un pont diviseur de tension.

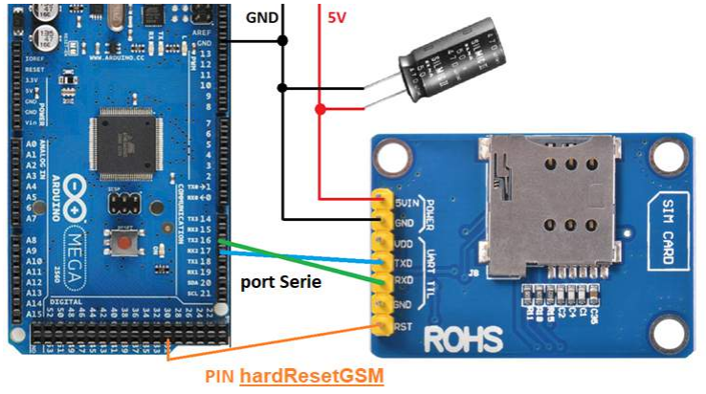
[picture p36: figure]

Page 11 sur 27

5. Gsm + hardResetGSM

Le GSM permet de vous envoyer des SMS quand il y a une anomalie détectée par l’AQUABOUNS. Il y a diffèrent modèle disponible, vérifier la tension de fonctionnement de celui-ci, 3.3V ou 5V. Personnellement j’utilise un sim800l fonctionnent en 5V.
Le module GSM communique avec l’AQUABOUNS via un port série de votre choix que vous devez configurer dans le logiciel.
Il faut connecter RX GSM sur TX Arduino et TX GSM sur RX Arduino (TX = transmission, RX = réception) et alimenter le GSM.
Le pin reset du GSM doit être connecté au pin de l’Arduino que vous aurez également configuré dans le logiciel.
Attention, le GSM a des pics de consommation, au moment de la recherche de réseau, pouvant atteindre 2A.
Il faut donc bien dimensionner son alimentation.
Vous ne devez pas alimenter l’écran par une sortie 5V de l’Arduino.
L’ajoute de condensateurs absorbera ces pics.

!!! TRES IMPORTANT !!!
Pour que la communication fonctionne, il est IMPERATIF que le GND de l’alimentions soit également relié à l’Arduino
!!! TRES IMPORTANT !!!

La valeur du condensateur sera peut-être à ajuster, pour ma part, j’utilise un 220uF.
Pour qu’il soit le plus efficace, il doit être le plus près possible du module.
ATTENTION, lors du montage à bien respecter la polarité du condensateur, UNE INVERSION DE POLARITÉ DU CONDENSATEUR ENGENDRE UNE EXPLOSION DU COMPOSANT.

Exemple de montage sur le port série 2 et reset sur le pin 31 :

Page 12 sur 27

6. nextion

L’écran tactile nous permet de d’interagir avec l’AQUABOUNS.
Plusieurs choix s’offrent à vous : taille 5" ou 7", version standard ou améliorée (processeur plus puissant, nu ou avec boitier selon le montage que vous souhaitez)

!!! TRES IMPORTANT !!!
Il faut impérativement utiliser un écran NEXTION ORIGINAL, les copies ne reconnaissent pas le fichier contenant le logiciel. Ils sont disponibles, entre autres, sur https://nextion.itead.cc/nextion-shop/!!! TRES IMPORTANT !!!

>>> Le principe de l'écran tactile résistif : deux couches en surfaces séparées par de minuscules entretoises et parcourues de connecteurs.
Le toucher du doigt ou d'une pointe quelconque déforme la surface supérieure et met en contact ses connecteurs avec ceux de la surface intérieure. L'utilisation d'un stylet est souvent nécessaire.

>>> Le principe de l'écran tactile capacitif : quand le doigt, conducteur d'électricité, touche l'écran, des charges électriques lui sont transférées. (Comme nos téléphones actuels)

Les modèles compatibles :
Écran 5" NX8048T050_011R <<< version standard résistif nue
Écran 5" NX8048K050_011R <<< version améliorée résistif nue
Écran 7" NX8048T070_011R <<< version standard résistif nue
Écran 7" NX8048K070_011R <<< version améliorée résistif nue
Écran 7" NX8048K070_011C <<< version améliorée capacitif avec boitier

Bon à savoir
Les écrans « standards » ne pourront afficher que les courbes PH + Température.
Les écrans « améliorées » afficheront les courbes PH + Température + Redox + Salinité.

Pour réaliser la connexion de l’écran Nextion à l’AQUABOUNS, il faut connecter RX Nextion sur TX Arduino et TX Nextion sur RX Arduino (TX = transmission, RX = réception) et alimenter l’écran. Attention l’écran consomme en moyenne 650mA avec des pics à 1A, vous ne devez pas alimenter l’écran par une sortie 5V de l’Arduino.

!!! TRES IMPORTANT !!!
Pour que la communication fonctionne, il est IMPERATIF que le GND de l’alimentions soit également relié à l’Arduino
!!! TRES IMPORTANT !!!

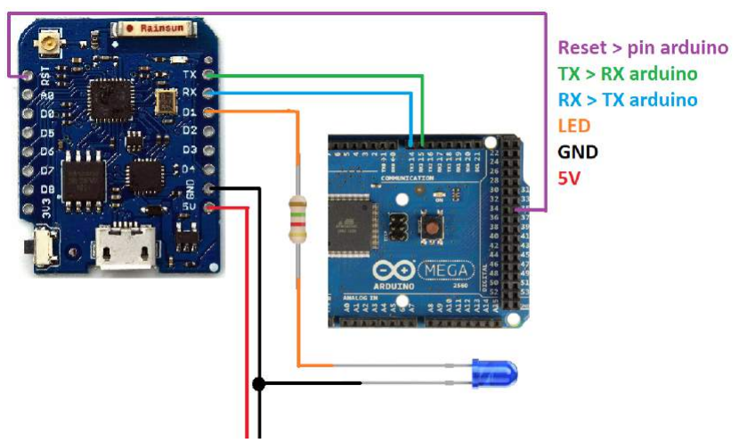
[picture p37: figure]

Page 13 sur 27

Exemple de montage sur le port série 1 :

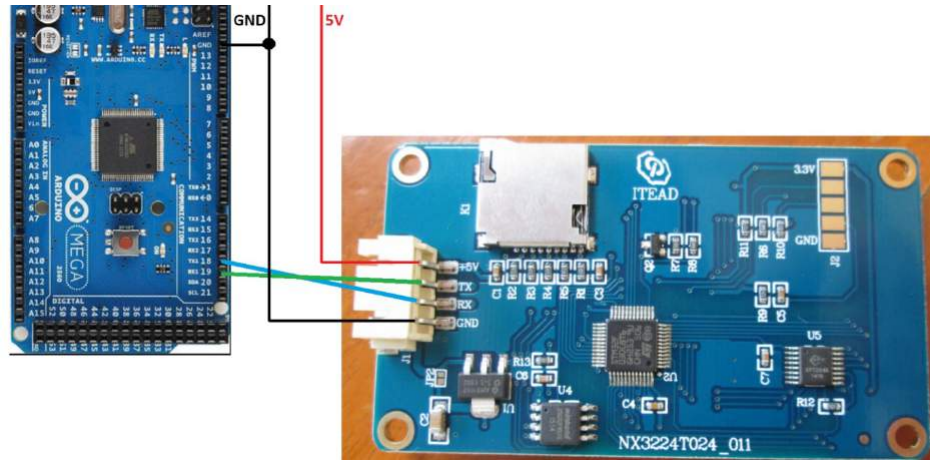
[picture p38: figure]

7. d1mini + hardResetWIFI

Le module D1 mini permet la connexion de l’AQUABOUNS à votre réseau Wifi afin de pouvoir visualiser sur une page WEB les valeurs de votre aquarium.

Astuce Pour garantir une meilleure connexion à votre réseau, optez pour un modèle avec une antenne déporter.

La LED sur le module permet de visualiser l’état de connexion Wifi, Allumée = connectée.
Si la LED de votre module n’est pas visible (dans un boitier par exemple) vous pouvez connecter une LED au module pour visualiser l’état de connexion Wifi, Allumée = connectée.

Exemple de câblage sur le port série 3 et reset sur pin 35 de l’Arduino (choix du port série et du pin reset à faire dans le programme)

Page 14 sur 27

Attention lors du montage à bien respecter la polarité de la LED.

La valeur de la résistance dépend de la LED utilisée mais une valeur de 1k (1000 Ohms) devrait être assez surdimensionnée pour vous permettre d’avoir un témoin lumineux sans être éblouie. Augmenter la valeur de la résistance pour diminuer la luminosité.

8. pinOutBrassage 1, 2 et 3 (sortie Pwm vers les pompes brassages)

L’AQUABOUNS peut contrôler votre brassage.
Pour cela, il vous faut dans un premier temps connaître le fonctionnement de votre pompe de brassage. 3 pompes différentes ont été testées avec succès.
> Pompe JEBAO / JECOD ancienne génération
> Pompe JEBAO / JECOD nouvelle génération
> Pompe TUNZE muni d’un contrôleur
N’hésitez pas à me contacter si vous avez réussi à Contrôler toutes autres pompes. Voici ci-dessous des exemples de montage pour ces 3 pompes.

Connexion de l’Arduino sur une pompe JEBAO ancienne génération :
Dessoudez le fil signal et connectez-le directement sur le PIN de l’Arduino.
Connectez un fil supplémentaire sur la masse/GND de la pompe et reliez l’autre extrémité du fil au GND de l’Arduino

Page 15 sur 27

Connexion de l’Arduino sur une pompe JEBAO nouvelle génération (moteur brushless) :
Il vous faut une carte contrôleur de moteur brushless dimmable en PWM 5V
Dessoudez les trois fils du moteur de la pompe du contrôleur en notant la lettre indiquée sur le circuit imprimé (U, V ou W)
Ressoudez les trois fils du moteur directement sur la carte contrôleur de moteur brushless Connectez la carte contrôleur de moteur brushless au PWM et au GND de l’Arduino

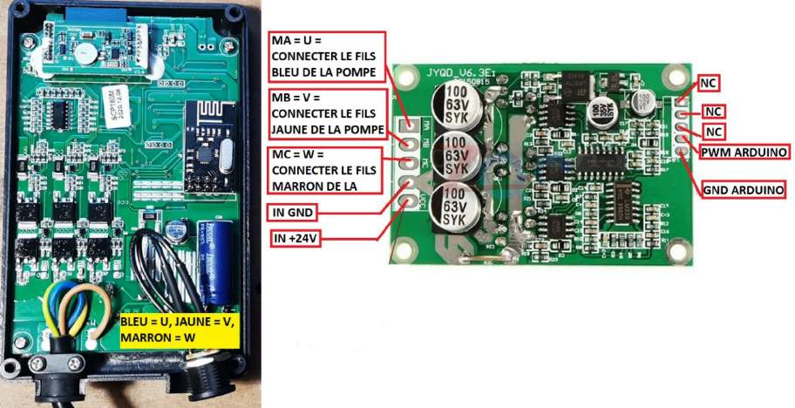
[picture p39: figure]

Connexion de l’Arduino sur une pompe TUNZE :
Avantage sur ces pompes il n’est pas nécessaire de « bricoler » la pompe mais il faut réaliser un petit montage électronique simple.
Il vous faut une diode Schottky, une résistance et un condensateur.
Les valeurs de la résistance et du condensateur seront peut-être à ajuster, pour ma part, j’utilise une 10k et un 470uF
Attention, lors du montage à bien respecter la polarité de la diode et surtout du condensateur. UNE INVERSION DE POLARITÉ DU CONDENSATEUR ENGENDRE UNE EXPLOSION DU COMPOSANT.

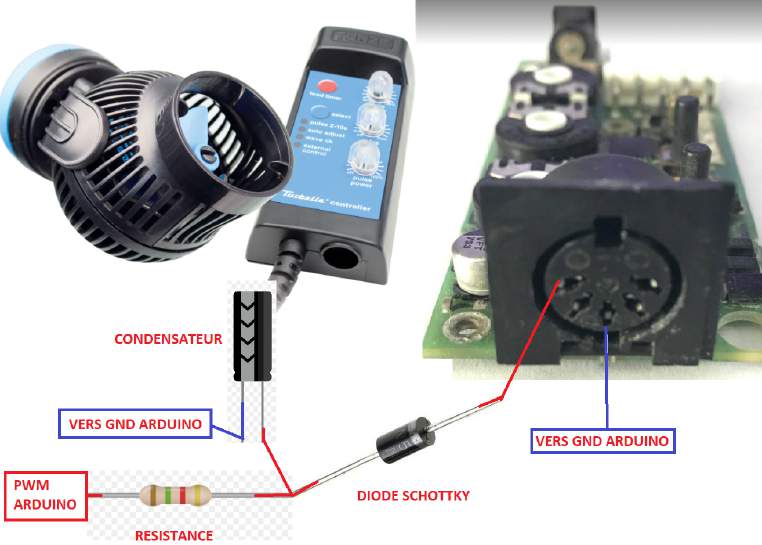
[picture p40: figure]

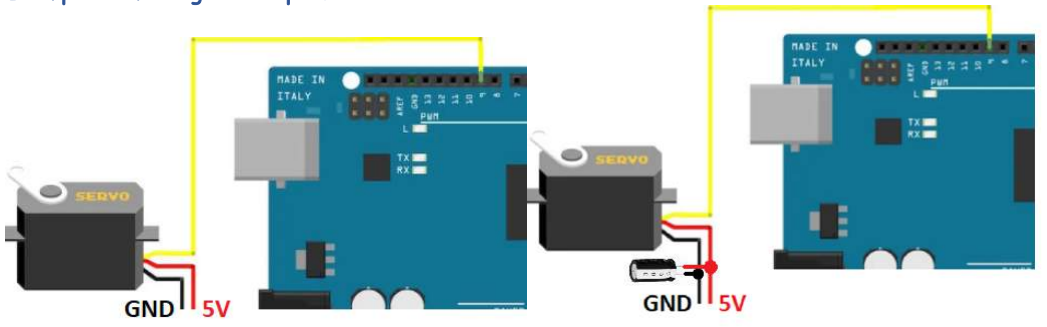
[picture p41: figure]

Page 16 sur 27

N’hésitez pas à me faire parvenir vos photos et explications pour toutes autres pompes de brassage, y compris si leur fonctionnement est régulé par un PWM d’une autre tension (10V par exemple), cela permettra d’étendre les possibilités pour les autres utilisateurs.

9. pinOUTOscillo 1, 2 et 3 (sortie Pwm vers les oscillateurs)

Connecter le servomoteur de votre oscillateur sur le pin que vous aurez configuré dans le logiciel et à votre alimentation.
Attention, votre servomoteur doit fonctionner en 5V.
S’il fait des mouvements anormaux, il faudra peut-être ajouter un condensateur 220uF
ATTENTION, Il y a une polarité sur le condensateur, UNE INVERSION DE POLARITÉ DU CONDENSATEUR ENGENDRE UNE EXPLOSION DU COMPOSANT

Exemple de montage sur le pin 9 de l’Arduino :

SANS condensateur | AVEC condensateur
10. pinOutEclairage 1, 2, 3 et 4 (sortie Pwm vers l’éclairage)

Votre éclairage peut être contrôlé par l’AQUABOUNS.
Pour cela, il vous faut connaitre le fonctionnement de driver de votre rampe LED : Ø Dimmable en PWM 5V
Ø Dimmable en 0-10V analogique
Ø Autre …

Une fois le mode de pilotage déterminé vous devrez :
Ø Pour les driver dimmable en PWM 5V, il suffit de connecter le driver au pin de l’Arduino que vous aurez configuré dans le logiciel.
Ø Pour les driver dimmable avec un signal analogique 0-10V, vous devez ajouter entre l’Arduino et le driver un module de conversion. La sortie analogique du module doit être connectée à la place de la sortie du potentiomètre.
La sortie GND doit être reliée la masse de la rampe.
Ø Pour les driver fonctionnant autrements, il faudras faire du cas par cas

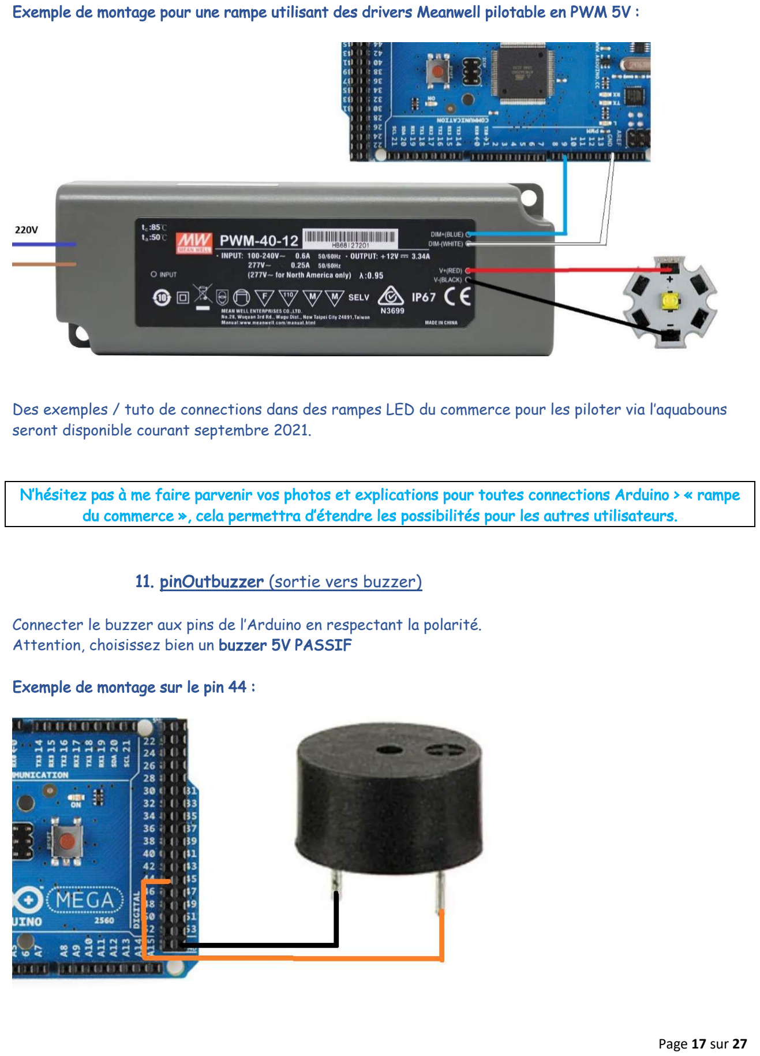
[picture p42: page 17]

Page 17 sur 27

Exemple de montage pour une rampe utilisant des drivers Meanwell pilotable en PWM 5V :

Des exemples / tuto de connections dans des rampes LED du commerce pour les piloter via l’aquabouns seront disponible courant septembre 2021.

N’hésitez pas à me faire parvenir vos photos et explications pour toutes connections Arduino > « rampe du commerce », cela permettra d’étendre les possibilités pour les autres utilisateurs.

11. pinOutbuzzer (sortie vers buzzer)

Connecter le buzzer aux pins de l’Arduino en respectant la polarité. Attention, choisissez bien un buzzer 5V PASSIF

Exemple de montage sur le pin 44 :

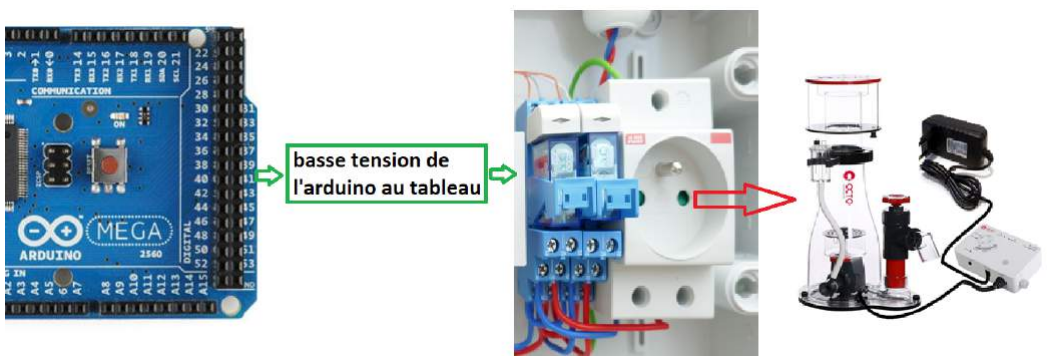
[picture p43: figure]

Page 18 sur 27

Le buzzer peut être totalement désactivé. Ce paramétrage est à faire sur la page « config.h » avant téléversement du code dans l’Arduino.

12. pinOutRelaisRemontee / pinOutRelaisChauffage / pinOutRelaisEcumeur / pinOutRelaisOsmolation / pinOutRelaisVentilateurBac / pinOutRelaisVentilateurRampe (sortie vers les relais)

Ces Pin active / désactive votre matériel (écumeur, pompe remontée, etc.) en fonction de divers paramètres et évènements survenu dans votre aquarium.
Ce matériel fonctionne majoritairement sur du 220V et toute intervention sur cette tension peux être dangereuse voire mortelle si elle n’est pas pratiquée par une personne expérimentée.

Je ne vous encourage pas à réaliser ce qui suit vous-même. Faite appel à un professionnel.

Je vais parler ici de 2 façons de monter des relais sur l’Arduino.
La première, celle que j’utilise, est la plus sécuritaire. C’est l’installation à privilégier !

Relais DIN :
Il s’agit de module DIN s’intégrant dans votre tableau électrique contenant un relais.
Le câblage Arduino / relais demande un montage électronique.
Cette installation a l’avantage de maintenir la tension dangereuse dans le tableau électrique avec des conditions de sécurité maximum.
C’est le montage qui a été fait sur le PCBouns (carte que j’ai réalisée, info en MP)

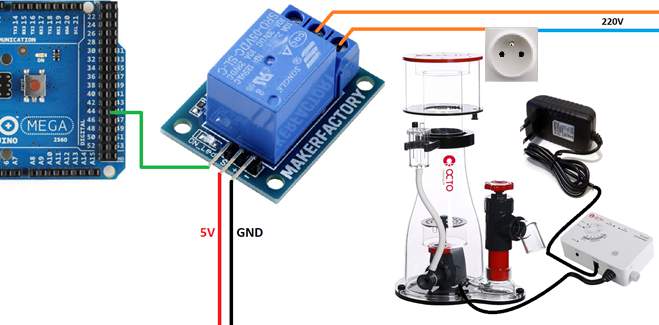
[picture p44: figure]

Page 19 sur 27

Carte relais :
Facile à trouver, facile à monter et pas chère, c’est la solution que la majorité d’entre vous adopteront, pourtant, c’est le montage comportant le plus de risque.

Exemple de montage sur le pin 45 pour le relais écumeur :

!!! TRES IMPORTANT !!!
Pour une raison de sécurité, le programme a été écrit de façon à ce que les éléments essentiels à votre aquarium ne soit pas coupé en cas de problème avec l’automate ou tout simplement dans le cas où il ne serait pas allumé ou connecté.
Cela nécessite d’inverser la connexion en sortie de relais.
Quels que soient les relais utilisés, vous devrez respecter le branchement ci-dessous sur la sortie du relais en fonction du matériel qui y sera connecté.
> Pompe de remontée | > Distributeur de nourriture
> Chauffage | > Pompe D’osmolation
> Ecumeur | > Ventilateur du Bac
| > Ventilateur de la rampe

Autre point important est de vérifier que votre relais est un "High Level Trigger" sans quoi le fonctionnement sera inversé.
High Level Trigger : signal sur le relais = relais fermé, pas de signal sur le relais = relais ouvert Low Level Trigger : signal sur le relais = relais ouvert, pas de signal sur le relais = relais fermé

Page 20 sur 27

13. pinInSondeDs18b20 (sondes de températures)

2 sondes ds18b20 peuvent être utilisées dans l’AQUABOUNS,
Datasheet : https://datasheets.maximintegrated.com/en/ds/DS18B20.pdf
Une résistance 4.7KOhms (4700 Ohms) est nécessaire et doit être connecter au 5V d’un côté et au fil « Data » (verte dans le schéma ci-dessous)

Exemple de montage :

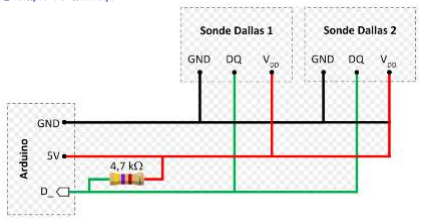
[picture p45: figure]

D_ correspond au pin de l’Arduino que vous avez choisi dans le programme pour connecter les sondes.

Pour la rampe,
La sonde doit être fixée au plus près du dissipateur de la rampe pour obtenir la valeur la plus réaliste et ainsi ventiler la rampe dès que la température devient trop élevée.
Plus votre rampe chauffe, plus la durée de vie des LED diminue et vice-versa.

Exemple de montage sur un dissipateur :

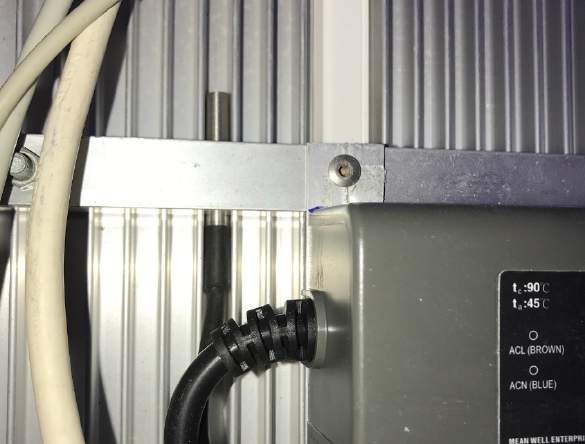
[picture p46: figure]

Pour l’eau de l’aquarium,
Je vous conseille d’être très prudent.
Il y a une multitude de sondes pour aquarium dont la qualité n’est pas au rendez-vous. Exemple avec cette sonde restée 2 mois dans mon aquarium marin :

Page 21 sur 27

Je vous déconseille donc d’utiliser ces sondes.
Tournez-vous vers une sonde ABS, un peu plus chère, mais cela vous évitera des tracas.
Exemple : https://www.lextronic.fr/capteur-de-teperature-ds18b20-ectanche-25138.html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

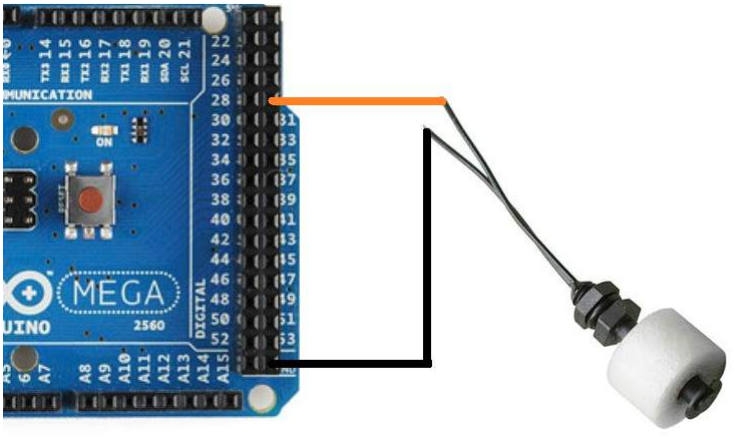
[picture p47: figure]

Page 22 sur 27

14. pinInFlotteurGodetEcumeur / pinInFlotteurReserve / pinInFlotteurOsmolation / pinInFlotteurNiveauEcumeur / pinInFlotteurSecurite (entrées des flotteurs)

Connecter un fil du flotteur au pin de l’Arduino et l’autre fil du flotteur au GND de l’Arduino. Exemple de montage d’un flotteur sur le pin 29 :

Dans le cas où vous n’utilisez pas un flotteur :
Ø Pour le flotteur du godet, connecter le Pin de l’Arduino au GND
Ø Pour le flotteur de la réserve, laisser le Pin vide
Ø Pour le flotteur de l’osmolation, connecter le Pin de l’Arduino au GND
Ø Pour le flotteur du niveau écumeur, connecter le Pin de l’Arduino au GND Ø Pour le flotteur de sécurité, connecter le Pin de l’Arduino au GND
15. pinOutRelaisDistributeurNouriture (sortie vers relais du distributeur)

Cette sortie actionne la distribution via un relais simulant le bouton manuel de votre distributeur Coté distributeur il va falloir souder un fils sur le bouton de distribution manuel pour le connecter au relais afin de simuler l’appuie sur le bouton.
Pour cela il faut ouvrir votre distributeur et repérer le bouton de déclanchement manuel.
Souder 1 fil sur l’entrée du bouton et l’autre sur la sortie.

Page 23 sur 27

Exemple avec un distributeur EHEIM Autofeeder 3581:

Puis connecter le distributeur au relais

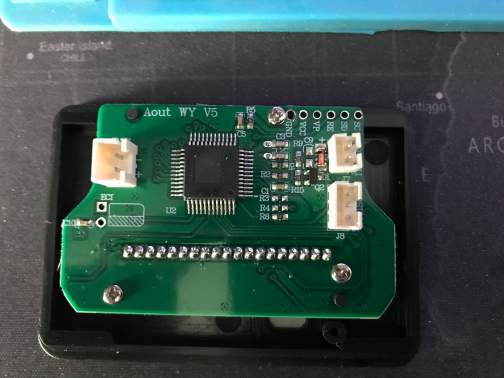
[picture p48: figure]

Page 24 sur 27

2e
exemple avec un distributeur « no name » de très bonne qualité, ultra silencieux. Vous pouvez le retrouver ici : https://amzn.to/2PKwDWl

Retirez les 4 vis sous l’appareil et ouvrez-le délicatement. :

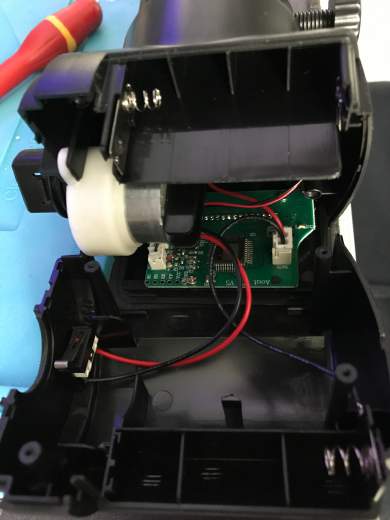
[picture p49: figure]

Déconnectez les 3 fils pour extraire le circuit imprimé puis retirez les 3 vis pour accéder à l’avant du circuit imprimé :

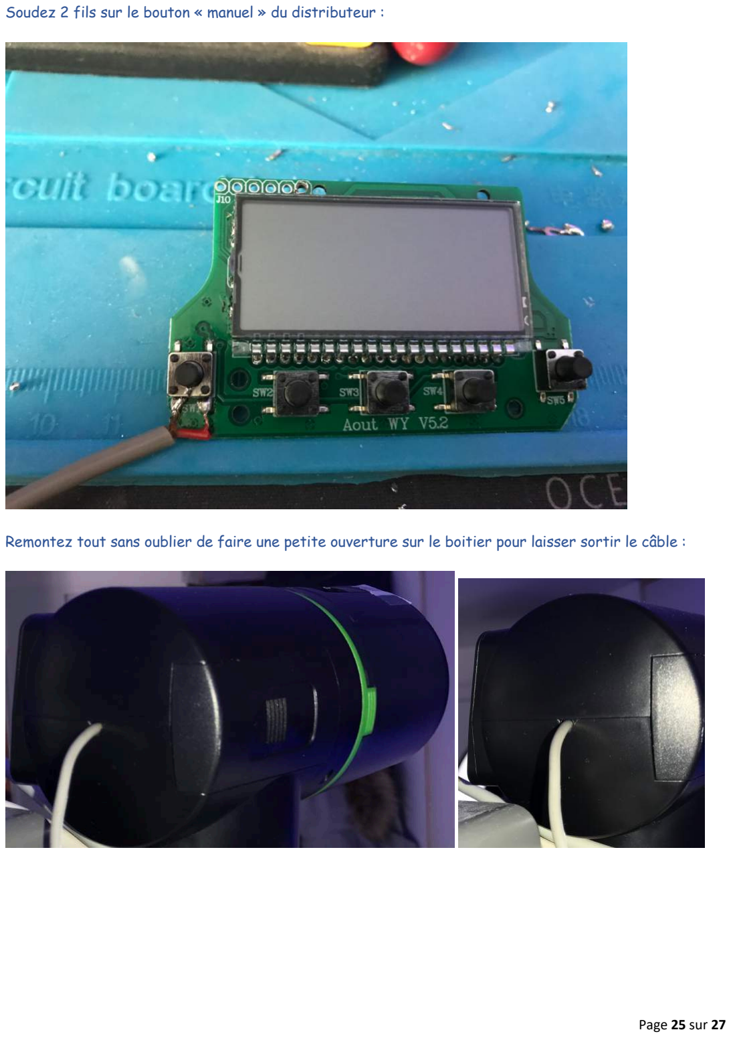
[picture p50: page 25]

Page 25 sur 27

Soudez 2 fils sur le bouton « manuel » du distributeur :

Remontez tout sans oublier de faire une petite ouverture sur le boitier pour laisser sortir le câble :

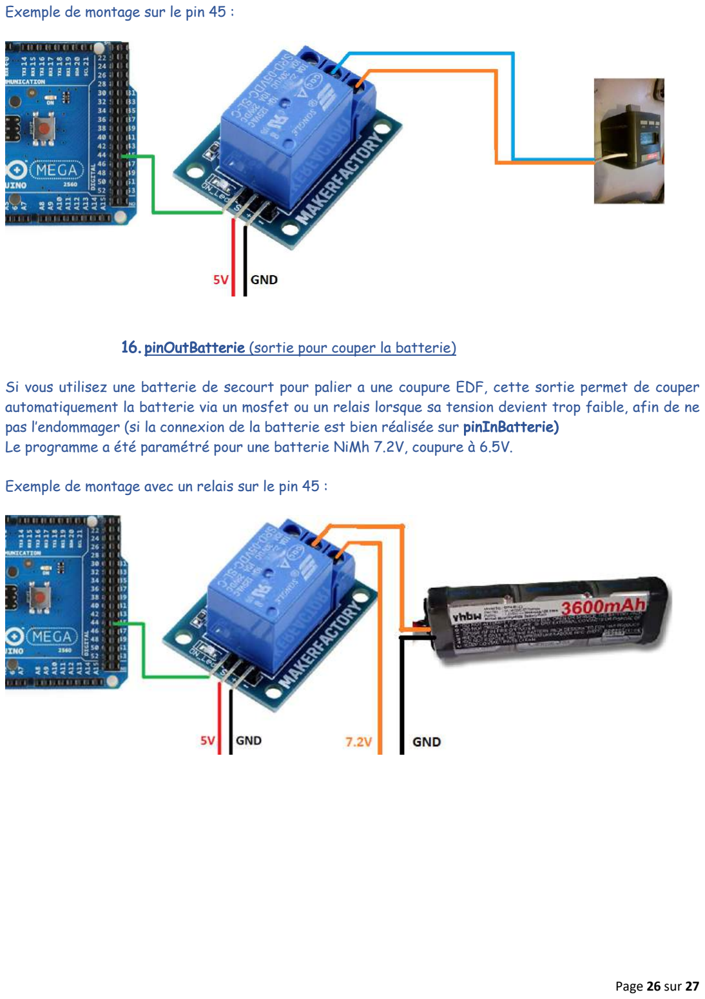
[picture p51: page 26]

Page 26 sur 27

Exemple de montage sur le pin 45 :

16. pinOutBatterie (sortie pour couper la batterie)

Si vous utilisez une batterie de secourt pour palier a une coupure EDF, cette sortie permet de couper automatiquement la batterie via un mosfet ou un relais lorsque sa tension devient trop faible, afin de ne pas l’endommager (si la connexion de la batterie est bien réalisée sur pinInBatterie)
Le programme a été paramétré pour une batterie NiMh 7.2V, coupure à 6.5V.

Exemple de montage avec un relais sur le pin 45 :

# I. A bientôt :

### Si le montage n’est pas à votre porté :

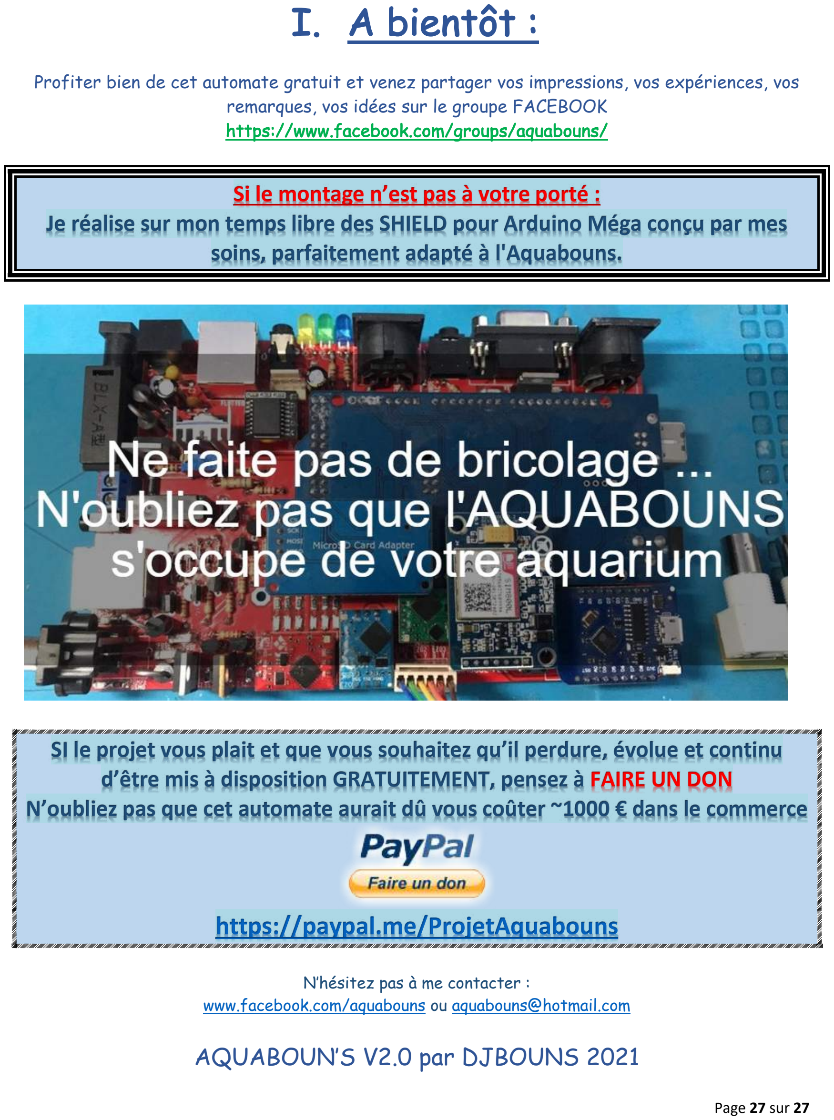
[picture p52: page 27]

Page 27 sur 27

Profiter bien de cet automate gratuit et venez partager vos impressions, vos expériences, vos remarques, vos idées sur le groupe FACEBOOK https://www.facebook.com/groups/aquabouns/

### Je réalise sur mon temps libre des SHIELD pour Arduino Méga conçu par mes

soins, parfaitement adapté à l'Aquabouns.

### SI le projet vous plait et que vous souhaitez qu’il perdure, évolue et continu d’être mis à disposition GRATUITEMENT, pensez à FAIRE UN DON N’oubliez pas que cet automate aurait dû vous coûter ~1000 € dans le commerce

## https://paypal.me/ProjetAquabouns

N’hésitez pas à me contacter : www.facebook.com/aquabouns ou aquabouns@hotmail.com

## AQUABOUN’S V2.0 par DJBOUNS 2021

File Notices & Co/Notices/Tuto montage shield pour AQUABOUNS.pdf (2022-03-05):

# Tuto exemple de montage d’un AQUABOUNS à partir d’un shield a borniers

Maj 03/09/21

## !!! ATTENTION !!!

Je ne suis pas électricien ni électronicien.
Ce qui suit n’est qu’un simple partage d’expérience. Toutes connexions/interfaces avec des tensions dangereuses ne doivent se faire que par du personnel qualifié et selon les normes en vigueur afin d’éviter tout risque d’accident ou d’incendie.
Ne pas laisser sans surveillance. Djbouns décline toute responsabilité quant aux dommages directs ou indirects qui pourraient être causés.

Bonjour, ce qui suit est un exemple de montage. Il n’engage que moi, temps sur la méthode que sur le matériel utilisé.

### SI le projet vous plait et que vous souhaitez qu’il perdure, évolue et continu d’être mis à disposition GRATUITEMENT, pensez à FAIRE UN DON N’oubliez pas que cet automate aurait dû vous coûter ~1000 € dans le commerce

## https://paypal.me/ProjetAquabouns

Différents liens sont présents pour vous aider. Les achats faits par ces liens participent également à soutenir le projet.

Les Liens suivis de * Correspondent à du matériel que j’utilise ou ai utilisés

# Merci d’avance J

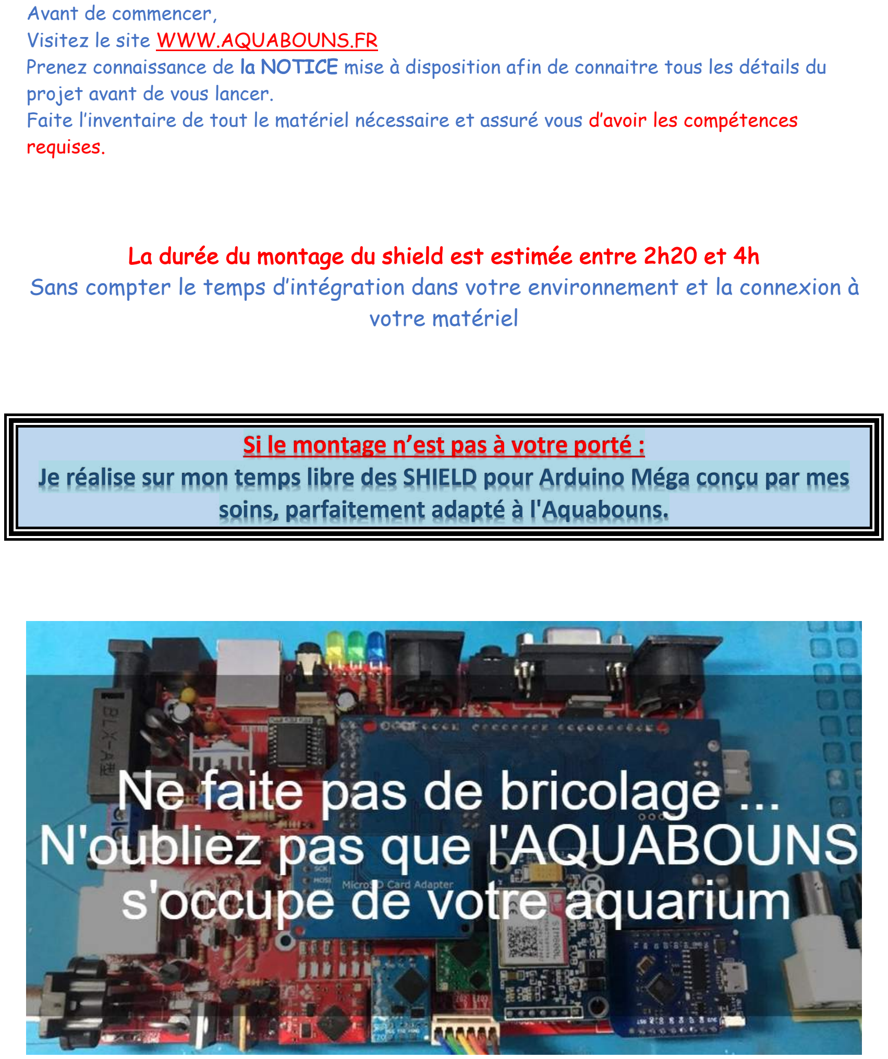
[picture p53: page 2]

Avant de commencer,
Visitez le site WWW.AQUABOUNS.FR
Prenez connaissance de la NOTICE mise à disposition afin de connaitre tous les détails du projet avant de vous lancer.
Faite l’inventaire de tout le matériel nécessaire et assuré vous d’avoir les compétences requises.

La durée du montage du shield est estimée entre 2h20 et 4h

### Sans compter le temps d’intégration dans votre environnement et la connexion à votre matériel

### Si le montage n’est pas à votre porté : Je réalise sur mon temps libre des SHIELD pour Arduino Méga conçu par mes

soins, parfaitement adapté à l'Aquabouns.

A. Outillage nécessaires :

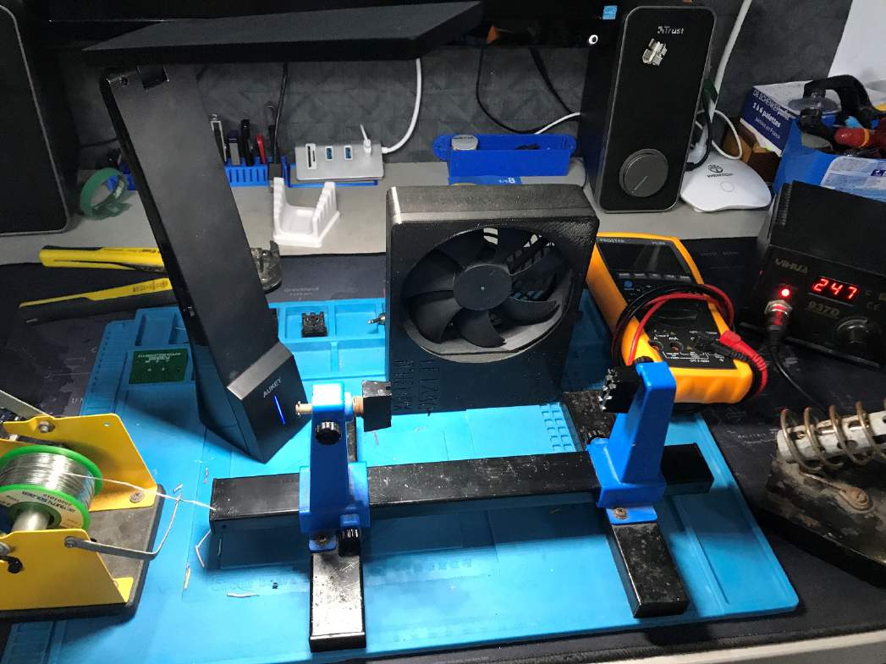
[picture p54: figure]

Un fer ou une station à souder : https://amzn.to/38zUTQQ
https://amzn.to/3BFjHDo *
https://amzn.to/3yFiknR *

Un ventilateur (pour éviter de respirer les vapeurs de soudure très nocive) : https://amzn.to/38DlP2a
https://amzn.to/343QZgW
https://amzn.to/3wHJ4CN *

De l’étain :
https://amzn.to/38DlRHk
https://amzn.to/3ucgmYg *

Une 3e main :
https://amzn.to/345hx1l *
https://amzn.to/3ubdStp
https://amzn.to/2QF7nRM *
https://amzn.to/3ufGku6

Tapis de protection :
https://amzn.to/3faI1oe *
https://amzn.to/345SMlo

Un multimètre :
https://amzn.to/3faYPLV *
https://amzn.to/3wqqTAL *
https://amzn.to/3u9Vi4P

Pince à dénuder :
https://amzn.to/3wslp8y
https://amzn.to/3yIxck3 *
https://amzn.to/3oHEGR2
https://amzn.to/3cG0qb5 *
B. Composants nécessaires dans le tuto:

Des pins mâle et femelle :
https://amzn.to/3oEsJeJ
https://amzn.to/3vdSKUL

Des connecteurs male femelle pour relais ou module Atlas : https://amzn.to/3uaj0xX *
https://amzn.to/2T73UMJ

Du fil ou des jumpper :
https://amzn.to/3f8Gq2f *
https://amzn.to/3wqBnA3
https://amzn.to/3oDUZhD
https://amzn.to/3v7Tafc
https://amzn.to/2Siy4vY

Circuit imprimé de prototypage : https://amzn.to/3oFyVTD
https://amzn.to/2Sf2CPm

Condensateurs 220uF :
https://amzn.to/3oDQ9Ri
https://amzn.to/3jEFc12

Résistances 4.7k Ohms 1/4w : https://amzn.to/2QF2yIc
https://amzn.to/3wqTYMC
C. Périphériques nécessaires dans le tuto:

Shield Arduino méga avec bornier à vis : https://amzn.to/3vcR1yY *
https://amzn.to/38DICuM

Arduino Méga ORIGINAL :
https://amzn.to/3veW5me

Arduino Méga copie :
https://amzn.to/38BuIJx *
https://amzn.to/3bKDh6K *

Alimentation 5V, 4A, 8A et 10A : https://amzn.to/3wmbCAQ
https://amzn.to/3v7bntn
https://amzn.to/3yuUpav *

Module GSM SIM800L V2.0 :
https://amzn.to/34adS25 *
https://amzn.to/3fFnsPP
https://amzn.to/2TdiItm

Module Wifi Wemos d1 mini : https://amzn.to/3fcP53Q *
https://amzn.to/2WLyHk3
https://amzn.to/2REGG0i
https://amzn.to/3taT0DH

Lecteur de Carte SD :
https://amzn.to/3vcMnB0 *
https://amzn.to/3yuAVmd

Horloge DS3231 :
https://amzn.to/3vbAD1y
https://amzn.to/3yEDXDd

Sonde de température DS18B20 : https://amzn.to/3fHNzG3
https://amzn.to/345TsHJ *
https://amzn.to/348vw6E

Buzzer 5V Passif :
https://amzn.to/3fcVJaw
https://amzn.to/3DT9CF9

Relais ( 4 ) :
https://amzn.to/3fbCe1N
https://amzn.to/3n0FP75 *

Relais ( 8 ) :
https://amzn.to/3yGkDWu *
https://amzn.to/3mWv1XF
https://amzn.to/3BIoDrn

Flotteurs :
https://amzn.to/3gZ8GVT
https://amzn.to/3hMzYzK *

ÉCRAN NEXTION :

5" basic :
https://amzn.to/3mYaAcZ

5" amélioré :
https://amzn.to/3DJvZww
https://amzn.to/3kNg9IF
https://amzn.to/2WVa4BM

7" basic :
https://amzn.to/2QGGvAT *
https://amzn.to/3DJb10U

7" amélioré résistif ou capacitif : https://amzn.to/3vewaeH *
https://amzn.to/3vCtx5T
D. Autres Périphériques :

Alimentation 12V 5A ou 10A (Pour alimenter pompe d'osmolation, ventilateur, ect...) : https://amzn.to/3v8sYB8 *
https://amzn.to/2ScIa1z

Chargeur de batterie NiMh :
https://amzn.to/34lM6QB
https://amzn.to/2QGrJtY

Batterie NiMh 7.2V de 2000mAh a 4500mAh : https://amzn.to/3wppomR *
https://amzn.to/347gwFR

Chargeur de batterie lithium : https://amzn.to/3gY6zSe
https://amzn.to/2SBh6JA
https://amzn.to/3fA2qna

Batterie lithium :
https://amzn.to/3i9KyRP
https://amzn.to/3fUeDC6

Circuit imprimé d’alimentation à partir d’une alimentation de PC : https://amzn.to/3fZQnyg
https://amzn.to/3pbmuiL

Convertisseur DC-DC 4A (Pour convertir le 12V ou la batterie en 5V par exemple) : https://amzn.to/3fcT0O6
https://amzn.to/3DK1ypV

Convertisseur PWM 5V/10V
https://amzn.to/2Sk3baM *
https://amzn.to/2QLDQ9g *

Pompe d'osmolation 12v :
https://amzn.to/3bMSrsf
https://amzn.to/3vgshpm | *
https://amzn.to/348ysjG | *

Ventilateur d'aquarium ventilateur 12V : https://amzn.to/2SgpU7E
https://amzn.to/3pyhCEx *
https://amzn.to/3fCgY4h
https://amzn.to/3bJYjmc

Sonde PH :
https://amzn.to/3fFML4m *
https://amzn.to/3uczDJo
https://amzn.to/3fdR8Vw *
https://amzn.to/3fb2cmj

Solution étalon PH :
https://amzn.to/3f9OHTz
https://amzn.to/3494tYE
https://amzn.to/3wsk4Pb *

Sonde ORP :
https://amzn.to/3oJtp2C *
https://amzn.to/3u7dRGJ

Solution étalon ORP :
https://amzn.to/3484qfH
https://amzn.to/3fzf0lg

Rallonge BNC :
https://amzn.to/2WUTr9n
https://amzn.to/3vdiosJ *

BRASSAGE :

Pompe TUNZE Turbelle nanostream : https://amzn.to/3oEm1pb
https://amzn.to/3yqMBGN *
https://amzn.to/3u6Rb9P *

Cable DIN 5 (Pour se brancher sur le boitier de contrôle TUNZE) : https://amzn.to/3vhYc92 *

Pompe de brassage JEBAO série SOW : https://amzn.to/3hMXSeK

Pompe de brassage JEBAO série RW : https://amzn.to/2QLCyLs *

Contrôleur brushless (Pour contrôler toutes pompes à moteur brushless) : https://amzn.to/345EVf2
https://amzn.to/3n0vCI6

Oscillateur :
https://neo3plus.com/fr/accessoires/203-oscillateurs-de-pompes-osci.html *

Module Atlas Scientific :
https://www.robesol.nl/en/atlas-scientific/
https://atlas-scientific.com/
https://www.whiteboxes.ch/cart/

Si vous avez Pris le shield déjà montée, passer à l’étape 2.

1. Assemblage du shield :
Durée : 20/30 min

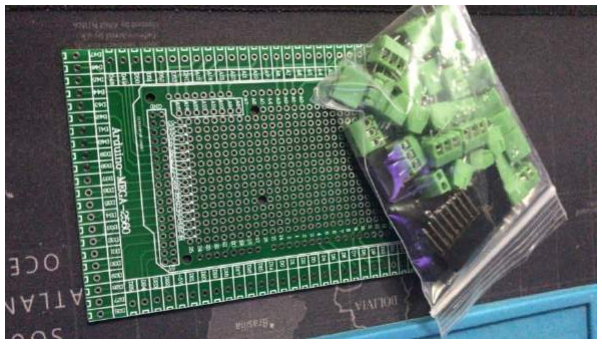
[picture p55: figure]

Commencé par souder le bouton SMD, car il vous sera très compliqué de le faire après. Soudez les pins traversants puis soudez les borniers

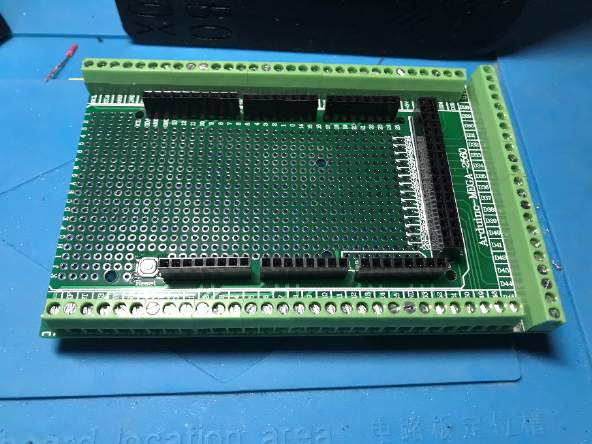
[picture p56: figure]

Vérifiez que l’Arduino S’emboite bien dedans (faite attention de ne pas tordre de pin)

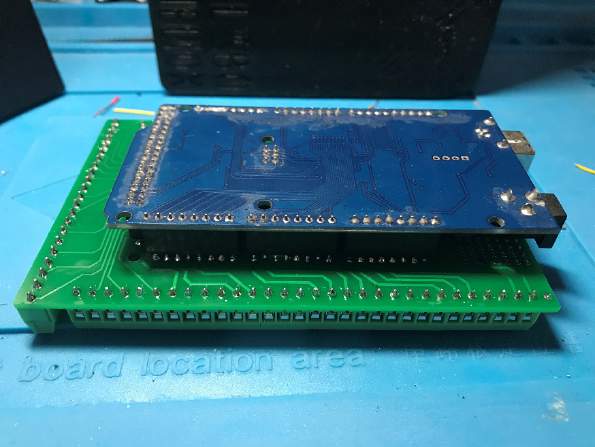
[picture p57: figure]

2. Placement des pins :
Durée : 20/30 min

En suivant le schéma ci-dessous :
Soudez les pins Mâles à l’emplacement bleu ciel
Soudez les pins Femelles aux emplacements rouges
Soudez une résistance 4.7k Ohms à l’emplacement orange
Soudez un condensateur 220uF 6.3V ou 16V à l’emplacement vert (ATTENTION, Il y a une polarité sur le condensateur, pour repérer le négatif, il y a une petite bande de couleur différente de haut en bas, la patte est également plus petite, UNE INVERSION DE POLARITÉ DU CONDENSATEUR ENGENDRE UNE EXPLOSION DU COMPOSANT) Soudez le buzzer à l’emplacement jaune (Attention à la polarité)

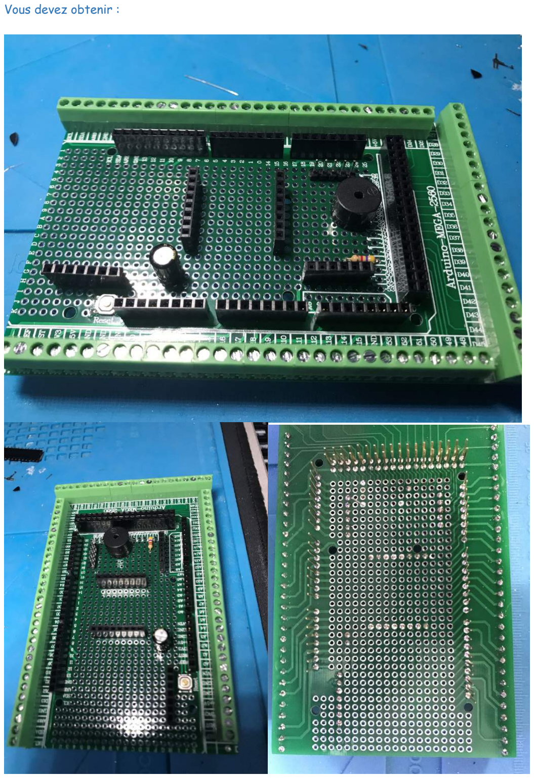
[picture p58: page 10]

Vous devez obtenir :

3. Connection de l’alimentation :
Durée : 45min/1h

Soudez des fils ou des jumper en suivant le schéma ci-dessous, rouge étant le 5V et le noir le GND (les pins gris sont inutilisés) :

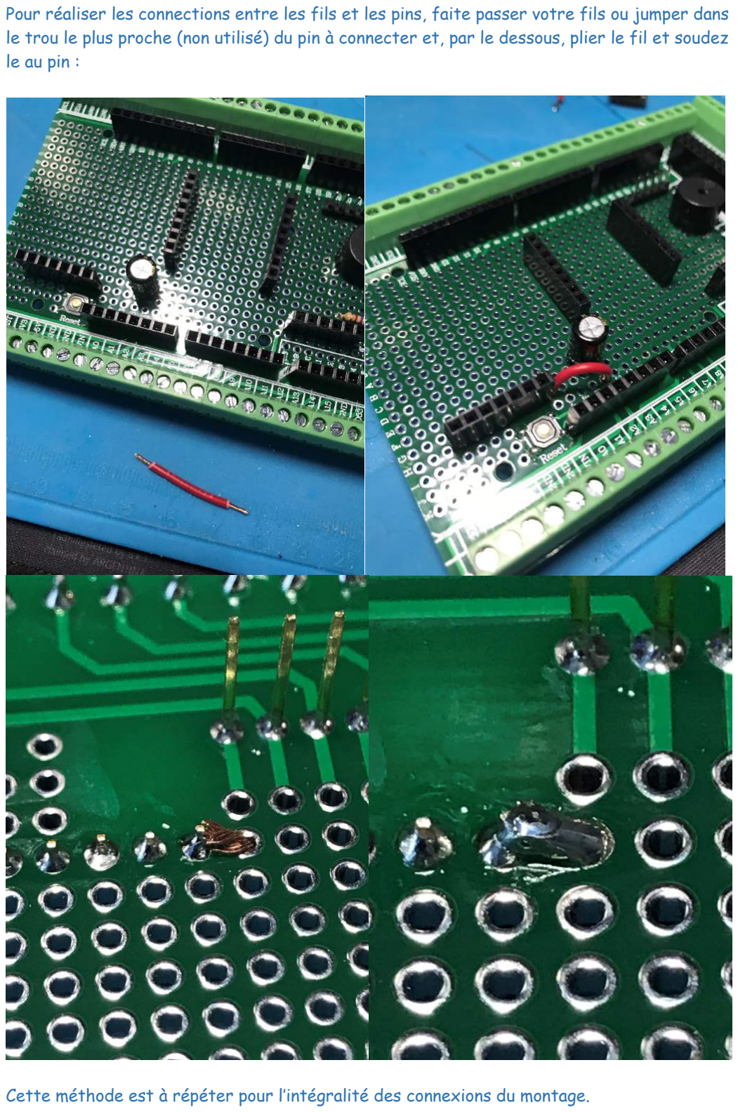
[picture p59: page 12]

Pour réaliser les connections entre les fils et les pins, faite passer votre fils ou jumper dans le trou le plus proche (non utilisé) du pin à connecter et, par le dessous, plier le fil et soudez le au pin :

Cette méthode est à répéter pour l’intégralité des connexions du montage.

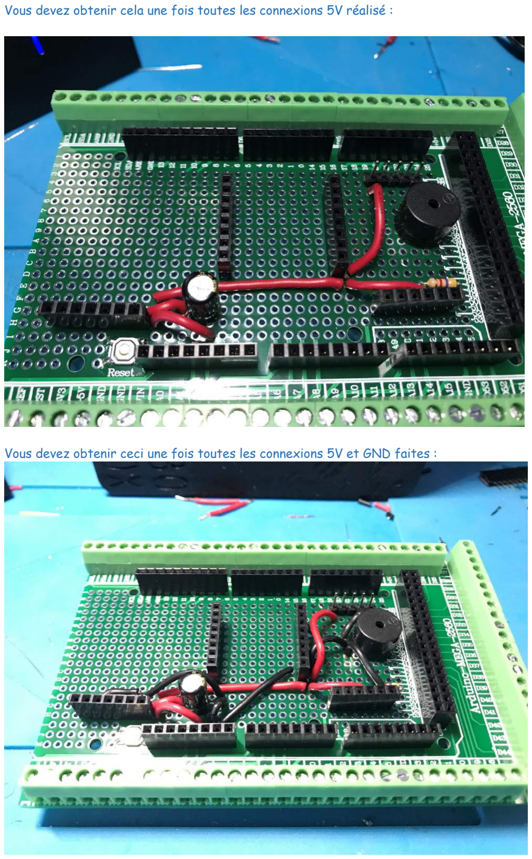
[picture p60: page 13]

Vous devez obtenir cela une fois toutes les connexions 5V réalisé :

Vous devez obtenir ceci une fois toutes les connexions 5V et GND faites :

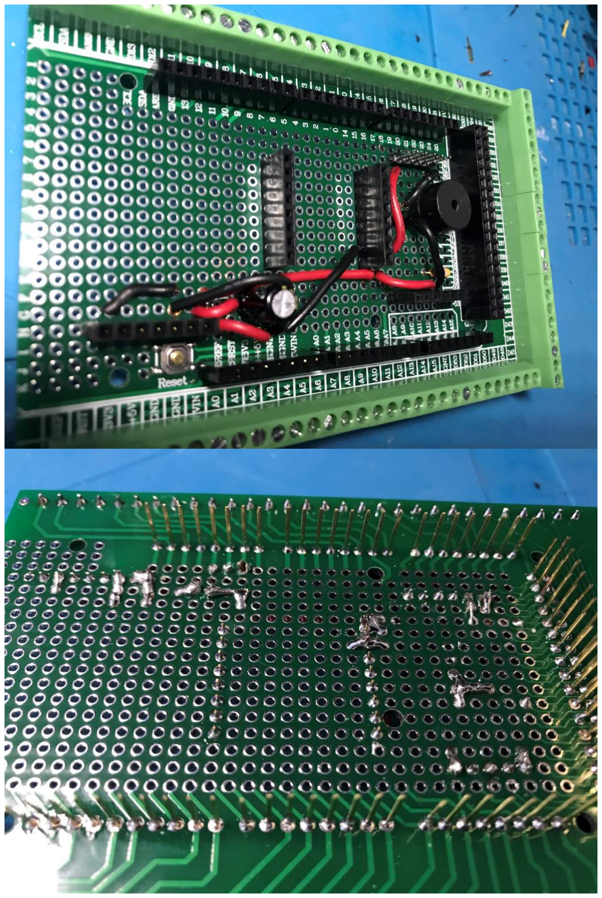
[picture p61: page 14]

4. Connexion des fils « data » aux pins de l’Arduino :
Durée : 45min/1h

Soudez les fils de data comme le schéma ci-dessous :

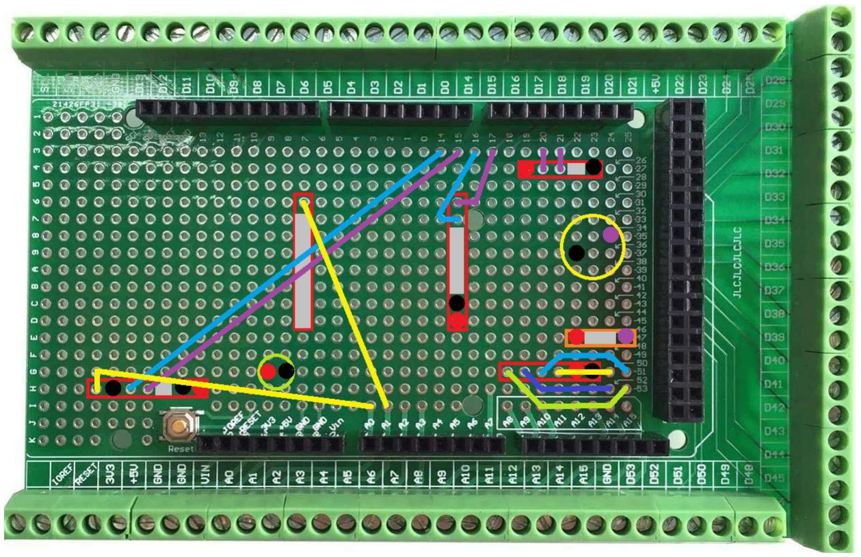
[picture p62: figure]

Vous devez obtenir ceci :

5. Vous avez fini les soudures sur le shield.

Vous pouvez connecter votre Arduino et vos périphériques. Voici à quoi cela doit ressembler :

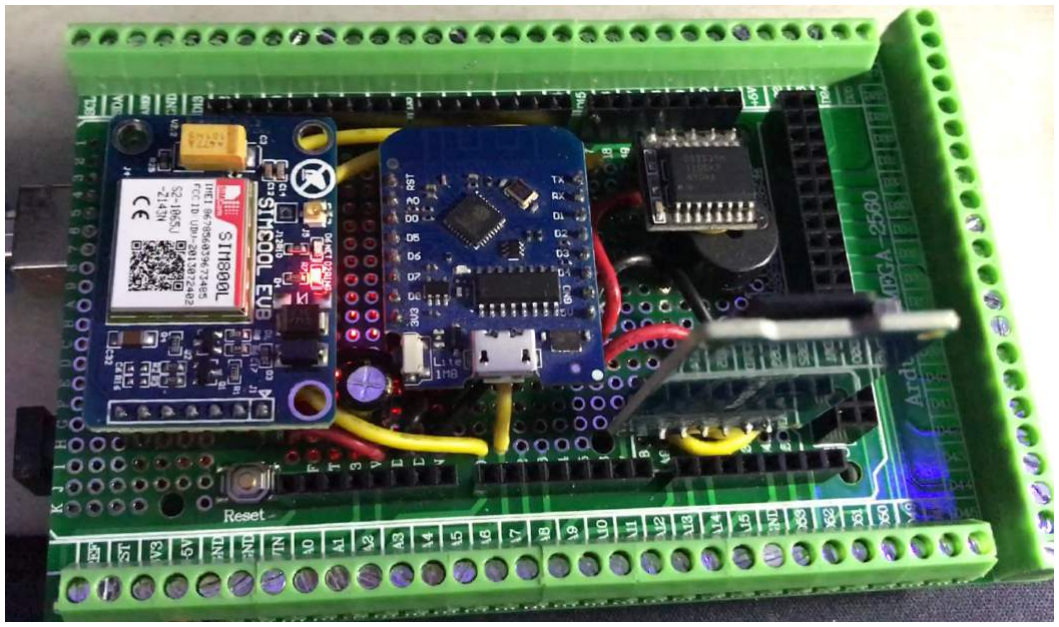
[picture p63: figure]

Pour plus d’information sur les différents composants que vous venez d’installer, consulter la fiche « notice d'installation et d'utilisation du programme Aquabouns V2.0.pdf » sur le site https://aquabouns.yolasite.com/notice.php

6. Alimentation et répartition du 5V et GND :
Durée : 5min

De nombreux périphériques vont utiliser le 5V et le GND.
Il vous sera impossible de tout connecter au bornier du shield.
J’utilise un PCB de prototypage pour faire cela. Vous pouvez aussi utiliser des dominos même si je ne suis pas fan.
Je découpe un petit morceau du PCB et je soude sur une ligne tout le 5V et plus loin tout le GND de mes périphériques et de mon alimentation principal, sans oublier d’ajouter un fils de chaque que je connecte au bornier correspondant.

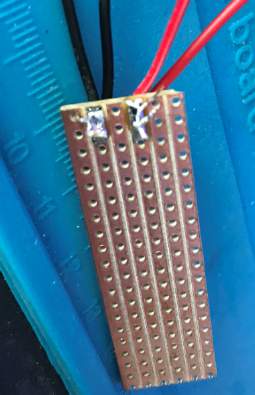
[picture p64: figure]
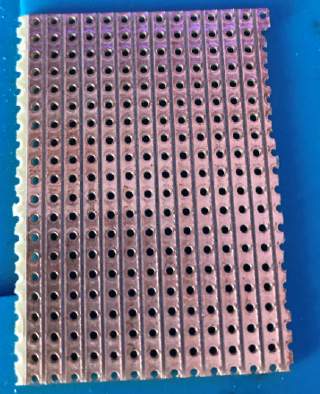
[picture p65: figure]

7. Connection des relais :
Durée : 5min/10min

Utiliser une nappes mâles / femelles
Coté relais, vous n’avez qu’as connecté sur les pins mâles :

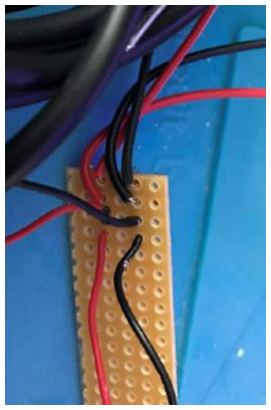
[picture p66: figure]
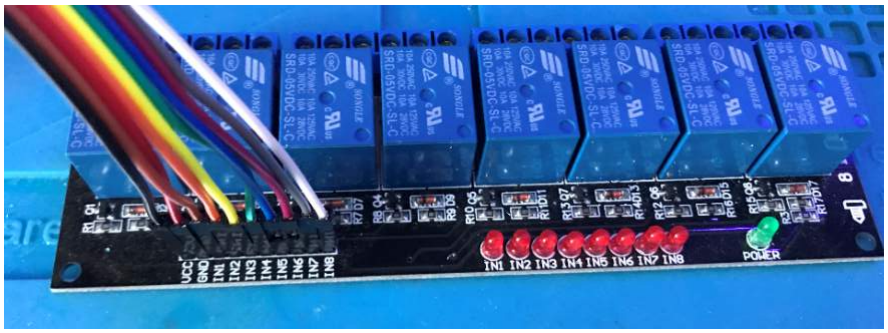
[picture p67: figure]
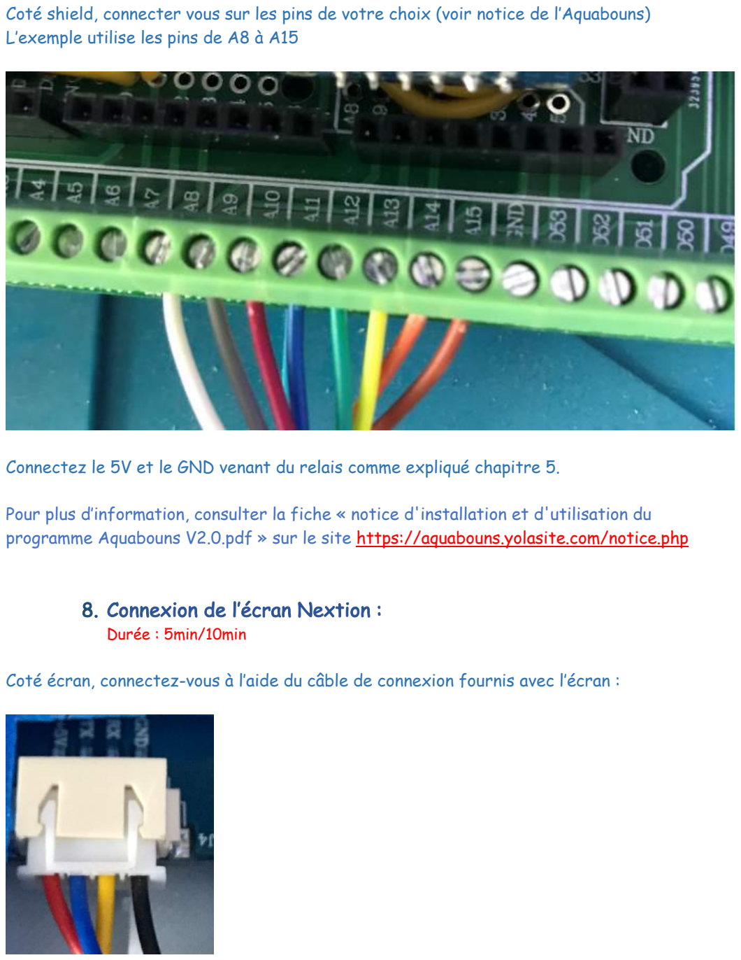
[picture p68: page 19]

Coté shield, connecter vous sur les pins de votre choix (voir notice de l’Aquabouns) L’exemple utilise les pins de A8 à A15

Connectez le 5V et le GND venant du relais comme expliqué chapitre 5.

Pour plus d’information, consulter la fiche « notice d'installation et d'utilisation du programme Aquabouns V2.0.pdf » sur le site https://aquabouns.yolasite.com/notice.php

8. Connexion de l’écran Nextion :
Durée : 5min/10min

Coté écran, connectez-vous à l’aide du câble de connexion fournis avec l’écran :

Coté shield, connectez-vous sur le port série restant = SERIAL1 = pin 18 et pin 19 Bien respecter la connexion jaune sur 18 et bleu sur 19


Connectez le 5V et le GND venant de l’écran comme expliqué chapitre 5.

Pour plus d’information, consulter la fiche « notice d'installation et d'utilisation du programme Aquabouns V2.0.pdf » sur le site https://aquabouns.yolasite.com/notice.php

9. Connexion des sondes de température DS18B20 :
Durée : 5min/10min

Soudez les fils jaune des deux sondes ensembles et connectez-les au pin 47 (pin ou est connecté la résistance 4.7K Ohms)


Connectez le 5V et le GND venant des sondes comme expliqué chapitre 5.

Pour plus d’information, consulter la fiche « notice d'installation et d'utilisation du programme Aquabouns V2.0.pdf » sur le site https://aquabouns.yolasite.com/notice.php

10. Connexion des flotteurs :
Durée : 5min/10min

Connectez un fils de chaque flotteur sur les pins de votre choix. Dans l’exemple, les flotteurs sont sur les pins de 38 à 42


Soudez le fil restant de chaque flotteur au GND comme expliqué chapitre 5.

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

11.Connexion Module Atlas :
Durée : 5min/10min

Pour les modules Atlas, je vous conseille fortement d’utiliser une carte déjà faite pour plusieurs raisons :
Ce sont des mesures de précision, tout montage hasardeux pourrait fausser les mesures. Extrait du datasheet :


J’ai également lu que toutes soudure sur les modules annuleras la garantis

Pour ces raisons, je vous conseille donc d’utiliser des cartes spécifiques, exemple : Carte 1 module non isolé : https://www.whiteboxes.ch/shop/ezo-carrier-board-non-isolated/
Carte 1 module isolé :
https://www.whiteboxes.ch/shop/electrically-isolated-usb-ezo-carrier-board-gen2/

Coté carte, connectez la carte à l’aide du câble fournie
Coté shield,
Ø Si vous avez plusieurs cartes, connecter tous les RX ensemble et tous les TX ensemble puis connectez les fils TX au pin 20 (SDA) et les fils RX au pin 21 (SCL)
Ø Si vous n’avez qu’une carte, connectez le fil TX au pin 20 (SDA) et le fil RX au pin 21 (SCL) Connectez le 5V et le GND venant des sondes comme expliqué chapitre 5.

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

12. Test
Durée : 5 min
Il est temps de faire un test pour vérifier que tout fonctionne.
Tout d’abord, téléverser le programme AQUABOUNS dans l’Arduino et dans le module Wifi en suivant toute les instructions de la notice disponible sur le site WWW.AQUABOUNS.FR Ensuite connecter sur le shield l’Arduino et tous les périphériques.
Brancher votre alimentation.
Ø Si tout se passe bien votre AQUABOUNS prend vie J
Ø Dans le cas contraire, couper immédiatement la source d'alimentation et vérifier votre montage qu'il n'y est pas de faux contact et revérifier toute vos connections avant de réessayer.

Bon à savoir :
Lors du premier démarrage,
Ø L'AQUABOUNS va vous signalez que l’horloge n’as jamais été initialisé.
Ø L'AQUABOUNS va créer des fichiers sur la carte.
Ø L’AQUABOUNS va importer les paramètres par défauts.
Ø S’il n'y a pas de carte SIM dans le module GSM, l'initialisation ne sera pas complète (de même si votre SIM est protégé pas un mot de passe. Vous devez supprimer le code PIN)
13. Connexion de votre matériel a l’Arduino
Durée : ?
Pour la connexion de votre matériel, oscillateur, brassage, éclairage, relais …, consulter la fiche « notice d'installation et d'utilisation du programme Aquabouns V2.0.pdf » sur le site https://aquabouns.yolasite.com/notice.php
14. Présence de l’alimentation et batterie :
Durée : ?

Vous devez brancher sur le pin libre de votre choix une source de courant, 5V MAX, pour signaler à l’Arduino qu’il est alimenté par votre source d’énergie principal.

L’Aquabouns permet d'être alerté en cas de coupure de courant.
Cela implique qu'il faut installer un system d'alimentation de secoure (batterie, onduleur etc...)
Cette partie n'est pas à la portée de tous puisque ce montage dépend du matériel utiliser par chacun (alimentation de l’Arduino + System de secours) et nécessite un montage électronique. Je ne donnerais donc aucune instruction à ce sujet.
Si cette partie du montage n’est pas réalisé, votre AQUABOUNS ne pourra pas vous prévenir en cas de coupure de courant.

15. Résolution de problèmes :
Durée : ?

Problème de fonctionnement entre les diffèrent composant :
>>> Vérifier que tous les GND sont commun. Même si vous utiliser plusieurs sources d’alimentation, les négatifs doivent être relié entre eux.

Problème de communication entre Arduino / D1 mini / Sim800l / écran Nextion :
>>> Vérifier vos connexions RX/TX. Il ne faut pas connecter RX avec RX et TX avec TX. Les connexions RX (réception) doivent être connectées au TX (transmission) du module opposé.

Servomoteur qui tremble :
>>> Manque de puissance d’alimentation. Le servomoteur ne doit pas être alimenté par le 5V de l’Arduino mais par une alimentation externe.
>>> Pic de consommation trop important. Ajouter un/des condensateur(s) sur l’alimentation juste avant le servomoteur, pour ma part, j’ai un 220uF.
>>> Servomoteur de mauvaise qualité / fatigué. J’ai personnellement eu le problème avec des copies de futaba s3003, en changeant le servomoteur, le problème a disparu sans modifier le montage.

Horloge DS3231 qui ne garde pas l'heure en mémoire après un redémarrage :
>>> La batterie de sauvegarde est vide. Changé la batterie si possible (certain model on la batterie soudé) IMPORTANT, vérifier bien la référence de la batterie / pile utilisé et replacer la par la même référence.

Si le montage n’est pas à votre porté :

### Je réalise sur mon temps libre des SHIELD pour Arduino Méga conçu par mes

soins, parfaitement adapté à l'Aquabouns.

commerce; https://paypal.me/ProjetAquabouns

### SI le projet vous plait et que vous souhaitez qu’il perdure, évolue et continu d’être mis à disposition GRATUITEMENT, pensez à FAIRE UN DON N’oubliez pas que cet automate aurait dû vous coûter ~1000 € dans le

N’hésitez pas à me contacter : www.facebook.com/aquabouns ou aquabouns@hotmail.com

Profiter bien de cet automate gratuit et venez partager vos impressions, vos expériences, vos remarques, vos idées sur le groupe FACEBOOK https://www.facebook.com/groups/aquabouns/

## DJBOUNS 2021

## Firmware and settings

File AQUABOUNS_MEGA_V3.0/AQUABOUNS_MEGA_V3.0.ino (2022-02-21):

/*               AAA                 QQQQQQQQQ     UUUUUUUU     UUUUUUUU           AAA               BBBBBBBBBBBBBBBBB        OOOOOOOOO     UUUUUUUU     UUUUUUUUNNNNNNNN        NNNNNNNN   SSSSSSSSSSSSSSS
                A:::A              QQ:::::::::QQ   U::::::U     U::::::U          A:::A              B::::::::::::::::B     OO:::::::::OO   U::::::U     U::::::UN:::::::N       N::::::N SS:::::::::::::::S
               A:::::A           QQ:::::::::::::QQ U::::::U     U::::::U         A:::::A             B::::::BBBBBB:::::B  OO:::::::::::::OO U::::::U     U::::::UN::::::::N      N::::::NS:::::SSSSSS::::::S
              A:::::::A         Q:::::::QQQ:::::::QUU:::::U     U:::::UU        A:::::::A            BB:::::B     B:::::BO:::::::OOO:::::::OUU:::::U     U:::::UUN:::::::::N     N::::::NS:::::S     SSSSSSS
             A:::::::::A        Q::::::O   Q::::::Q U:::::U     U:::::U        A:::::::::A             B::::B     B:::::BO::::::O   O::::::O U:::::U     U:::::U N::::::::::N    N::::::NS:::::S
            A:::::A:::::A       Q:::::O     Q:::::Q U:::::D     D:::::U       A:::::A:::::A            B::::B     B:::::BO:::::O     O:::::O U:::::D     D:::::U N:::::::::::N   N::::::NS:::::S
           A:::::A A:::::A      Q:::::O     Q:::::Q U:::::D     D:::::U      A:::::A A:::::A           B::::BBBBBB:::::B O:::::O     O:::::O U:::::D     D:::::U N:::::::N::::N  N::::::N S::::SSSS
          A:::::A   A:::::A     Q:::::O     Q:::::Q U:::::D     D:::::U     A:::::A   A:::::A          B:::::::::::::BB  O:::::O     O:::::O U:::::D     D:::::U N::::::N N::::N N::::::N  SS::::::SSSSS
         A:::::A     A:::::A    Q:::::O     Q:::::Q U:::::D     D:::::U    A:::::A     A:::::A         B::::BBBBBB:::::B O:::::O     O:::::O U:::::D     D:::::U N::::::N  N::::N:::::::N    SSS::::::::SS
        A:::::AAAAAAAAA:::::A   Q:::::O     Q:::::Q U:::::D     D:::::U   A:::::AAAAAAAAA:::::A        B::::B     B:::::BO:::::O     O:::::O U:::::D     D:::::U N::::::N   N:::::::::::N       SSSSSS::::S
       A:::::::::::::::::::::A  Q:::::O  QQQQ:::::Q U:::::D     D:::::U  A:::::::::::::::::::::A       B::::B     B:::::BO:::::O     O:::::O U:::::D     D:::::U N::::::N    N::::::::::N            S:::::S
      A:::::AAAAAAAAAAAAA:::::A Q::::::O Q::::::::Q U::::::U   U::::::U A:::::AAAAAAAAAAAAA:::::A      B::::B     B:::::BO::::::O   O::::::O U::::::U   U::::::U N::::::N     N:::::::::N            S:::::S
     A:::::A             A:::::AQ:::::::QQ::::::::Q U:::::::UUU:::::::UA:::::A             A:::::A   BB:::::BBBBBB::::::BO:::::::OOO:::::::O U:::::::UUU:::::::U N::::::N      N::::::::NSSSSSSS     S:::::S
    A:::::A               A:::::AQQ::::::::::::::Q   UU:::::::::::::UUA:::::A               A:::::A  B:::::::::::::::::B  OO:::::::::::::OO   UU:::::::::::::UU  N::::::N       N:::::::NS::::::SSSSSS:::::S
    A:::::A                 A:::::A QQ:::::::::::Q      UU:::::::::UU A:::::A                A:::::A B::::::::::::::::B     OO:::::::::OO       UU:::::::::UU    N::::::N        N::::::NS:::::::::::::::SS
    AAAAAAA                 AAAAAAA  QQQQQQQQ::::QQ       UUUUUUUUU   AAAAAAA                 AAAAAAABBBBBBBBBBBBBBBBB        OOOOOOOOO           UUUUUUUUU      NNNNNNNN         NNNNNNN SSSSSSSSSSSSSSS
                                           Q:::::Q
                                            QQQQQQ
                                                                                              ad888888b,         ,a888a,
                                                                                             d8"     "88       ,8P"' `"Y8,
                                                                                                     a88      ,8P       Y8,
                                                                                                    ,88P      88         88
                                                                                                  aad8"       88         88
                                                                                                  ""Y8,       88         88
                                                                                                    `88b      88         88
                                                                                                     "88      `8b       d8'
                                                                                             Y8,     a88  d8b  `8ba, ,ad8'
                                                                                              "Y888888P'  Y8P    "Y888P"



                                                                                                     du 20/02/2022
                                                                                                         

                                                                             Le programme GRATUIT pour automatiser votre aquarium récifal
                                                                                         Créé par Djbouns, Copyright (C) 2022

                                                                            Avec l'aide du forum https://forum.arduino.cc pour le codage
                                                                                      Un grand merci particulierement a J.M.L
                                                                      Merci a Commodore D. pour tout les echanges qui ont fait grandire le projet

                                                             Et un grand merci a celui qui a redesigner toute la partie graphique de cette Aquabouns V3.0
                                                                                     !!!!!!!!!! Loïc 'Solyum' D. !!!!!!!!!!
                                                                                     Pour voir son travail ou le contacter:
                                                                                         https://www.behance.net/solyum
                                                                                       contact: loic_dekeyser@outlook.com



  //                              !!!!!!!!!!!!!!!!!!!!!!!!!!!!!!!!!!!!!!!!!!!!!!!!!!!!!!!!!!!!!!!!!!!!!!!!!!!!!!!!!!!!!!!!!!!!!!!!!!!!!!!!!!!!!!!!!!!!!!!!!!!!!!!!!!!!!!!!!!!!!!!!!!!!!!*/

//                                                      !!!!! Soutenez le projet pour qu'il continu d’évoluer et d’êtres mis a disposition gratuitement !!!!!
//                                                                            https://www.paypal.com/donate/?hosted_button_id=HWQ5X3M39VEP4

//                              !!!!!!!!!!!!!!!!!!!!!!!!!!!!!!!!!!!!!!!!!!!!!!!!!!!!!!!!!!!!!!!!!!!!!!!!!!!!!!!!!!!!!!!!!!!!!!!!!!!!!!!!!!!!!!!!!!!!!!!!!!!!!!!!!!!!!!!!!!!!!!!!!!!!!!



/* Ce programme est un logiciel libre: vous pouvez le redistribuer
  et/ou le modifier selon les termes de la "GNU General Public
  License", tels que publiés par la "Free Software Foundation"; soit
  la version 2 de cette licence ou (à votre choix) toute version
  ultérieure.

  Ce programme est distribué dans l'espoir qu'il sera utile, mais
  SANS AUCUNE GARANTIE, ni explicite ni implicite; sans même les
  garanties de commercialisation ou d'adaptation dans un but spécifique.

  Se référer à la "GNU General Public License" pour plus de détails.
  Vous la trouverez dans l'onglet GNU_General_Public_License.h
  Ou sur http://www.gnu.org/licenses/

  Vous devriez avoir reçu une copie de la "GNU General Public License"
  en même temps que ce programme; sinon, écrivez a la "Free Software
  Foundation, Inc., 675 Mass Ave, Cambridge, MA 02139, USA".*/



//$$$$$$$$$$$$$$$$$$$$$$$$$$$$$$$$$$$$$$$$$$$$$$$$$$$$$$$$$$$$$$$$$$$$$$$$$$$$$$$$$$$$$$$$$$$ Librairies $$$$$$$$$$$$$$$$$$$$$$$$$$$$$$$$$$$$$$$$$$$$$$$$$$$$$$$$$$$$$$$$$$$$$$$$$$$$$$$$$$$$$$$$$$$
#include <Wire.h>
#include <OneWire.h>
#include "Ezo_i2c.h"
#include <avr/wdt.h>
#include <avr/pgmspace.h>
#include <EEPROM.h>
#include "DallasTemperature.h"
#include "Nextion.h"

//$$$$$$$$$$$$$$$$$$$$$$$$$$$$$$$$$$$$$$$$$$$$$$$$$$$$$$$$$$$$$$$$$$$$$$$$$$$$$$$$$$$$$$$$$$$ Fichiers $$$$$$$$$$$$$$$$$$$$$$$$$$$$$$$$$$$$$$$$$$$$$$$$$$$$$$$$$$$$$$$$$$$$$$$$$$$$$$$$$$$$$$$$$$$
#include "config.h"
#include "global.h"
#include "affichage.h"
#include "autres.h"
#include "brassage.h"
#include "debug.h"
#include "eclairage.h"
#include "eeprom.h"
#include "flotteurs.h"
#include "gsm.h"
#include "horloge.h"
#include "oscillo.h"
#include "carteSD.h"
#include "temperature_ph.h"
#include "wifi.h"

//$$$$$$$$$$$$$$$$$$$$$$$$$$$$$$$$$$$$$$$$$$$$$$$$$$$$$$$$$$$$$$$$$$$$$$$$$$$$$$$$$$$$$$$$$$$ Déclarations $$$$$$$$$$$$$$$$$$$$$$$$$$$$$$$$$$$$$$$$$$$$$$$$$$$$$$$$$$$$$$$$$$$$$$$$$$$$$$$$$$$$$$$$$$$
uint32_t roulementPrecedent1;
uint8_t roulement1 = 0;
uint8_t roulement2 = 1;
const uint16_t refreshSwitch = 1000;

/* texte en PROGMEM pour SMS, Ecran et SD */
const char texteNextionDemarrage[] PROGMEM = "Demarrage, chargement des parametres";
const char smsAlerteSecuriteDecante[] PROGMEM = " Niveau securite decante, ecumeur + osmolateur OFF";
const char smsCoupureEdf[] PROGMEM = " Coupure EDF";
const char smsDegree[] PROGMEM = " degree";
const char smsEdfOk[] PROGMEM = " EDF OK";
const char smsGodetPlein[] PROGMEM = " Godet plein, ecumeur OFF";
const char smsOsmolationOk[] PROGMEM = " Osmolation ON";
const char smsPh[] PROGMEM = " Ph : ";
const char smsReserveVide[] PROGMEM = " Reserve vide";
const char smsSecuriteDecanteOk[] PROGMEM = " Niveau securite decante OK";
const char smsTemperature[] PROGMEM = " Temperature : ";
const char smsTropOsmolation[] PROGMEM = " Trop de declenchement de l'osmolateur, osmolateur OFF";
const char smsTropRemplissage[] PROGMEM = " temps de remplissage depasse";
const char texteNextionAlerte[] PROGMEM = "ALERTE ";
const char texteAlerteActuellement[] PROGMEM = "Actuellement ";
const char texteNextionAquaRampe[] PROGMEM = "Aqua/Rampe"; // texte stocker en progmem
const char texteNextionAucuneReponseGsm[] PROGMEM = "Aucune reponse du module Gsm !!!";
const char texteNextionAucuneReponseSD[] PROGMEM = "Aucune reponse de la carte SD !!!";
const char texteNextionAucuneReponseWifi[] PROGMEM = "Aucune reponse du module Wifi !!!";
const char texteNextionAucuneSonde[] PROGMEM = "Aucune sonde de temperature detectee !!!";
const char texteNextionBIENVENUE[] PROGMEM = "BIENVENUE";
const char texteNextionDANS[] PROGMEM = "DANS";
const char texteNextionLAQUABOUNS[] PROGMEM = "L'AQUABOUN'S";
const char texteNextionVersion[] PROGMEM = "V3.0";
const char texteNextionTemperatureBac[] PROGMEM = "ALERTE TEMPERATURE"; // texte stocker en progmem
const char texteNextionDeuxSonde[] PROGMEM = "DEUX sondes de temperature detectees, OK !";
const char texteNextionErreurModeRoutage[] PROGMEM = "Erreur de passage en mode routage !!!";
const char texteNextionErreurModeTexte[] PROGMEM = "Erreur de passage en mode texte !!!";
const char texteNextionFinAlerte[] PROGMEM = "Fin d'alerte,";
const char texteNextionHorlogeDetectee[] PROGMEM = "l'Horloge a ete detectee";
const char texteNextionHorlogeJamaisInitialise[] PROGMEM = "Horloge jamais initialise ou plus de batterie !";
const char texteNextionImportationDe[] PROGMEM = "Importation de ";
const char texteNextionImportationEepromDefault[] PROGMEM = "Importation des parametres par default, OK !";
const char texteNextionImportationEepromOK[] PROGMEM = "Importation des parametres de l'eeprom, OK !";
const char texteNextionInitialisationGsm[] PROGMEM = "Initialisation du module Gsm ... ";
const char texteNextionInitialisationGsmOK[] PROGMEM = "Initialisation du module Gsm, OK !";
const char texteNextionInitialisationHorloge[] PROGMEM = "Initialisation de l'Horloge... ";
const char texteNextionInitialisationHorlogeOK[] PROGMEM = "Initialisation de l'Horloge, OK !";
const char texteNextionInitialisationSD[] PROGMEM = "Initialisation de la carte SD... ";
const char texteNextionInitialisationSDOK[] PROGMEM = "Initialisation du lecteur de carte SD, OK !";
const char texteNextionInitialisationSonde[] PROGMEM = "Initialisation des sondes de temperature ... ";
const char texteNextionInitialisationWifi[] PROGMEM = "Initialisation du module Wifi ...";
const char texteNextionInitialisationWifiOK[] PROGMEM = "Initialisation du module Wifi, OK !";
const char texteNextionModuleNonDetecte[] PROGMEM = "Module non detecte !!!"; // texte stocker en progmem
const char texteNextionNonConnecte[] PROGMEM = "Non connecte"; // texte stocker en progmem
const char texteNextionPasDeFichier[] PROGMEM = "Pas de fichier ";
const char texteNextionPasDeReponseHorloge[] PROGMEM = "Pas de reponse de l'Horloge !!!";
const char texteNextionUneSonde[] PROGMEM = "UNE sonde de temperature detectee, OK !";
const char texteSurSDDemarrage[] PROGMEM = "DEMARRAGE DE L'AQUABOUNS";
const char texteSurSDRedemarrage[] PROGMEM = "REDEMARRAGE MANUEL DE L'AQUABOUNS";
const char texteVide[] PROGMEM = ""; // texte stocker en progmem
const char finDuFichier[] PROGMEM = "*.*.*.*.*.* FIN DU FICHIER *.*.*.*.*.*"; // texte stocker en progmem
const char osg0[] PROGMEM = "o,sg,0"; // texte stocker en progmem
const char otds0[] PROGMEM = "o,tds,0"; // texte stocker en progmem
const char oec0[] PROGMEM = "o,ec,0"; // texte stocker en progmem
const char os1[] PROGMEM = "o,s,1"; // texte stocker en progmem

#ifdef DEBUG // si en mode debug
const uint16_t delaisPourMoyene = 10000;
uint32_t compteurDelaisPourMoyene;
uint16_t nombre2Loop;
boolean printNombre2Loop = false;
#endif

//$$$$$$$$$$$$$$$$$$$$$$$$$$$$$$$$$$$$$$$$$$$$$$$$$$$$$$$$$$$$$$$$$$$$$$$$$$$$$$$$$$$$$$$$$$$ Fonction $$$$$$$$$$$$$$$$$$$$$$$$$$$$$$$$$$$$$$$$$$$$$$$$$$$$$$$$$$$$$$$$$$$$$$$$$$$$$$$$$$$$$$$$$$$
void loopDesFonctions() {
  if (millis() - roulementPrecedent1 > refreshSwitch) { // si compteur ateind
    roulementPrecedent1 = millis(); // reinitialise le compteur
    roulement1++; // increment
    rafraichirHeureSiSurMenu(); // rafraichi l'heure
    horaire(); // recupere heure de l'horloge
    flotteurs(); // lance la fonction
    oscillateur(); // lance la fonction
    coupureEdf(); // lance la fonction
    tempeteAleatoireAutomatique(); /* declanche la tempete aleatoire si activé */
    nourrissage(); /* declanche le nourissage si activé */
    rebootAlarme(); /* reboot les alarme toutes les heures durant la periode d'alerte determiné */
    if (pageActuelNextion == orph) { // si pas sur la page
      etalonnageEnCours();  // lance la fonction
    }
    if (progressionPuissanceBrassage) { // si progression ON
      progressionPuissanceBrassage = false;
      brassage();  // lance la fonction
      rafraichirBrassage1Nextion();  // lance la fonction
      rafraichirBrassage2Nextion(); // lance la fonction
      rafraichirBrassage3Nextion(); // lance la fonction
    }
    if (roulement1 == 3) { // quand compteur ateint
      roulement1 = 0;
      if (pageActuelNextion != orph) {
        salinite();  // lance la fonction
        if (pageActuelNextion == menu) {
          if (etaitEnEtalonnage) {
            attenteMesureSalinite();
          }
        }
      }
      switch (roulement2) {
        case 1:
          eclairage();
          rafraichirEclairageCouleur1Nextion();
          break;
        case 2:
          rafraichirEclairageCouleur2Nextion();
          break;
        case 3:
          rafraichirEclairageCouleur3Nextion();
          break;
        case 4:
          rafraichirEclairageCouleur4Nextion();
          temperature();
          break;
        case 5:
          rafraichirTemperatureBacNextion();
          break;
        case 6:
          rafraichirTemperatureRampeNextion();
          refuge();
          break;
        case 7:
          if (pageActuelNextion != orph) {
            ph();
          }
          break;
        case 8:
          if (pageActuelNextion != orph) {
            redox();
          }
          break;
        case 9:
          if (pageActuelNextion != orph) {
            rafraichirSaliniteNextion();
          }
          break;
        case 10:
          brassage();
          rafraichirBrassage1Nextion();
          break;
        case 11:
          rafraichirBrassage2Nextion();
          break;
        case 12:
          rafraichirBrassage3Nextion();
          stockLesMesures(); /* pour stocker les mesures temperature et ph sur sd */
          break;
        case 13:
          if (pageActuelNextion == menu) {
            rafraichirIconeBatterie();
          }
          coupureBatterie();
          roulement2 = 0;
          break;
      }
      roulement2++;
    }
  }
}
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
void loop() {
  lectureBoutons(); /* lis les bontons du nextion >>> !!! IMPORTANT !!! >>> loop minimum 450/seconde pour ne pas avoir de bouton sans reponse <<< !!! IMPORTANT !!! <<< */
  ecouterModuleWifi(); /* ecoute les demande du module wifi */
  loopDesFonctions(); // lance des fonctions secondaire a tour de role
  attenteMesurePH(); // attend la reception des mesures
  attenteMesureRedox(); // attend la reception des mesures
  attenteMesureSalinite(); // attend la reception des mesures
  wdt_reset(); // indique que le loop est OK, pas de bug, remise a zero du compteur "reboot" du watchdog

#ifdef TestSpeed
  if ((millis() - compteurDelaisPourMoyene) <= delaisPourMoyene) {
    nombre2Loop++;
    printNombre2Loop = true;
    DPRINTF(" watchdog reboot");  DPRINTLN();
  }
  else if (printNombre2Loop == true) {
    compteurDelaisPourMoyene = millis();
    DPRINTF(">>>>>>>>>>>>>>>>>>>>>>>>>>>>>>>>>>>>>>>>>>>>>>>>>>>>>>>>> printNombre2Loop : "); DPRINT(nombre2Loop / 10);  DPRINTLN();
    nombre2Loop = 0;
    printNombre2Loop = false;
  }
#endif

}

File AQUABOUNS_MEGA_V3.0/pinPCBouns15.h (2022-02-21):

#ifndef PinPCBouns15_h
#define PinPCBouns15_h

//$$$$$$$$$$$$$$$$$$$$$$$$$$$$$$$$$$$$$$$$$$$$$$$$$$$$$$$$$$$$$$$$$$$$$$$$$$$$$$$$$$$$$$$$$$$ Librairies $$$$$$$$$$$$$$$$$$$$$$$$$$$$$$$$$$$$$$$$$$$$$$$$$$$$$$$$$$$$$$$$$$$$$$$$$$$$$$$$$$$$$$$$$$$
#include <arduino.h>

//$$$$$$$$$$$$$$$$$$$$$$$$$$$$$$$$$$$$$$$$$$$$$$$$$$$$$$$$$$$$$$$$$$$$$$$$$$$$$$$$$$$$$$$$$$$ Déclarations $$$$$$$$$$$$$$$$$$$$$$$$$$$$$$$$$$$$$$$$$$$$$$$$$$$$$$$$$$$$$$$$$$$$$$$$$$$$$$$$$$$$$$$$$$$
/*


   Affectation des pin correspondant a l'utilisation du shield pour arduino mega PCBouns V1.5



  888b    888 8888888888      8888888b.  888     888     888  .d8888b.       88888888888 .d88888b.  888     888  .d8888b.  888    888 8888888888 8888888b.
  8888b   888 888             888   Y88b 888     888     888 d88P  Y88b          888    d88P" "Y88b 888     888 d88P  Y88b 888    888 888        888   Y88b
  88888b  888 888             888    888 888     888     888 Y88b.               888    888     888 888     888 888    888 888    888 888        888    888
  888Y88b 888 8888888         888   d88P 888     888     888  "Y888b.            888    888     888 888     888 888        8888888888 8888888    888   d88P
  888 Y88b888 888             8888888P"  888     888     888     "Y88b.          888    888     888 888     888 888        888    888 888        8888888P"
  888  Y88888 888             888        888     888     888       "888          888    888     888 888     888 888    888 888    888 888        888 T88b
  888   Y8888 888             888        888     Y88b. .d88P Y88b  d88P          888    Y88b. .d88P Y88b. .d88P Y88b  d88P 888    888 888        888  T88b
  888    Y888 8888888888      888        88888888 "Y88888P"   "Y8888P"           888     "Y88888P"   "Y88888P"   "Y8888P"  888    888 8888888888 888   T88b

                   d8888      8888888b.     d8888 8888888b. 88888888888 8888888 8888888b.       8888888b.  d8b 8888888 .d8888b. 8888888
                  d88888      888   Y88b   d88888 888   Y88b    888       888   888   Y88b      888  "Y88b 88    888  d88P  Y88b  888
                 d88P888      888    888  d88P888 888    888    888       888   888    888      888    888       888  888    888  888
                d88P 888      888   d88P d88P 888 888   d88P    888       888   888   d88P      888    888       888  888         888
               d88P  888      8888888P" d88P  888 8888888P"     888       888   8888888P"       888    888       888  888         888
              d88P   888      888      d88P   888 888 T88b      888       888   888 T88b        888    888       888  888    888  888
             d8888888888      888     d8888888888 888  T88b     888       888   888  T88b       888  .d88P       888  Y88b  d88P  888
            d88P     888      888    d88P     888 888   T88b    888     8888888 888   T88b      8888888P"      8888888 "Y8888P" 8888888
*/
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

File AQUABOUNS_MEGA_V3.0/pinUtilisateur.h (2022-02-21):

#ifndef PinUtilisateur_h
#define PinUtilisateur_h

//$$$$$$$$$$$$$$$$$$$$$$$$$$$$$$$$$$$$$$$$$$$$$$$$$$$$$$$$$$$$$$$$$$$$$$$$$$$$$$$$$$$$$$$$$$$ Librairies $$$$$$$$$$$$$$$$$$$$$$$$$$$$$$$$$$$$$$$$$$$$$$$$$$$$$$$$$$$$$$$$$$$$$$$$$$$$$$$$$$$$$$$$$$$
#include <arduino.h>

//$$$$$$$$$$$$$$$$$$$$$$$$$$$$$$$$$$$$$$$$$$$$$$$$$$$$$$$$$$$$$$$$$$$$$$$$$$$$$$$$$$$$$$$$$$$ Déclarations $$$$$$$$$$$$$$$$$$$$$$$$$$$$$$$$$$$$$$$$$$$$$$$$$$$$$$$$$$$$$$$$$$$$$$$$$$$$$$$$$$$$$$$$$$$
// entrées/sorties analogique
const uint8_t hardResetWIFI = A5; // reset du wifi
const uint8_t hardResetGSM = A6; // reset du gsm
const uint8_t pinInCoupureCourant = A7; // entree presence tension d'alimentation
const uint8_t pinInBatterie = A8; // entree niveau batterie
const uint8_t pinOutRelaisChauffage = A10; // relais coupure chauffage // ouvert = ON
const uint8_t pinOutRelaisEcumeur = A11; // relais ecumeur // ouvert = ON
const uint8_t pinOutRelaisRemontee = A13; // relais coupure remontee // ouvert = ON

//entrées/sorties digital
const uint8_t pinOutBrassage[3] {2, 3, 4}; // sortie Pwmpompe Brassage 1
const uint8_t pinOUTOscillo1 = 5; // sortie PWM ocsillateur Brassage 1
const uint8_t pinOUTOscillo2 = 6; // sortie PWM ocsillateur Brassage 2
const uint8_t pinOUTOscillo3 = 7; // sortie PWM ocsillateur Brassage 3
const uint8_t pinOutRelaisVentilateurRampe = 8; // relais ventilateur rampe
const uint8_t pinOutEclairage[4] {11, 12, 9, 10}; // sortie PWM eclairage Couleur1, color2, Couleur1, color2
#define pinInSondeDs18b20 13 // entree sonde temperature aquarium + rampe
#define nextion Serial1  // pin18 = tx1 + pin19 = rx1 >>> attention !!! la definition du port serie est a declarer dans la biblioteque NEXTION, fichier "NexConfig.h" ligne 37 !!!  la modification dans le code arduino est sans effet !!!
#define gsm Serial2 // pin18 = tx16 + pin17 = rx2
#define d1mini Serial3 // pin14 = tx3 + pin15 = rx3 
//20 sda > ds3231 + 3x MODUL ATLAS
//21 scl > ds3231 + 3x MODUL ATLAS
const uint8_t pinInFlotteurGodetEcumeur = 27; // entree flotteur godet ecumeur (ferme = ON)
const uint8_t pinOutRelaisRefuge = 28; // relais coupure refuge // ouvert = off
const uint8_t pinInFlotteurReserveBas = 29; // entree flotteur niveau bas reserve d'eau (ferme si niveau bas reserve d'eau osmose)
const uint8_t pinOutRelaisRemplissageReserve = 30; // relais ou electrovanne pour remplissage reserve
const uint8_t pinInFlotteurReserveHaut = 31; // entree flotteur disponible, non utilisé pour le momment
const uint8_t pinOutRAC = 32; // relais ou electrovanne pour RAC
const uint8_t pinInFlotteurOsmolation = 33; // entree flotteur osmolation (ferme = ON)
const uint8_t pinInFlotteurNiveauEcumeur = 35; // entree flotteur niveau ecumeur (ferme = ON)
const uint8_t pinOutRelaisDistributeurNouriture = 37; // relais distributeur nouriture
const uint8_t pinInFlotteurSecurite = 39;// entree flotteur securité decante (ouvert si niveau haut decante)
const uint8_t pinOutBatterie = 41; // relais distributeur nouriture
const uint8_t pinOutRelaisVentilateurBac = 47; // relais ventilateur bac
const uint8_t pinOutbuzzer = 48; // sortie buzzer 48
const uint8_t pinOutRelaisOsmolation = 49; // relais pompe osmolation
//50 miso > carte sd
//51 mosi > carte sd
//52 sck > carte sd
#define SD_CS_PIN // pin53  > carte sd

#endif
